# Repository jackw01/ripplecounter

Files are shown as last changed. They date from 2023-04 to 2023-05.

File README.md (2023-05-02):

# ripplecounter

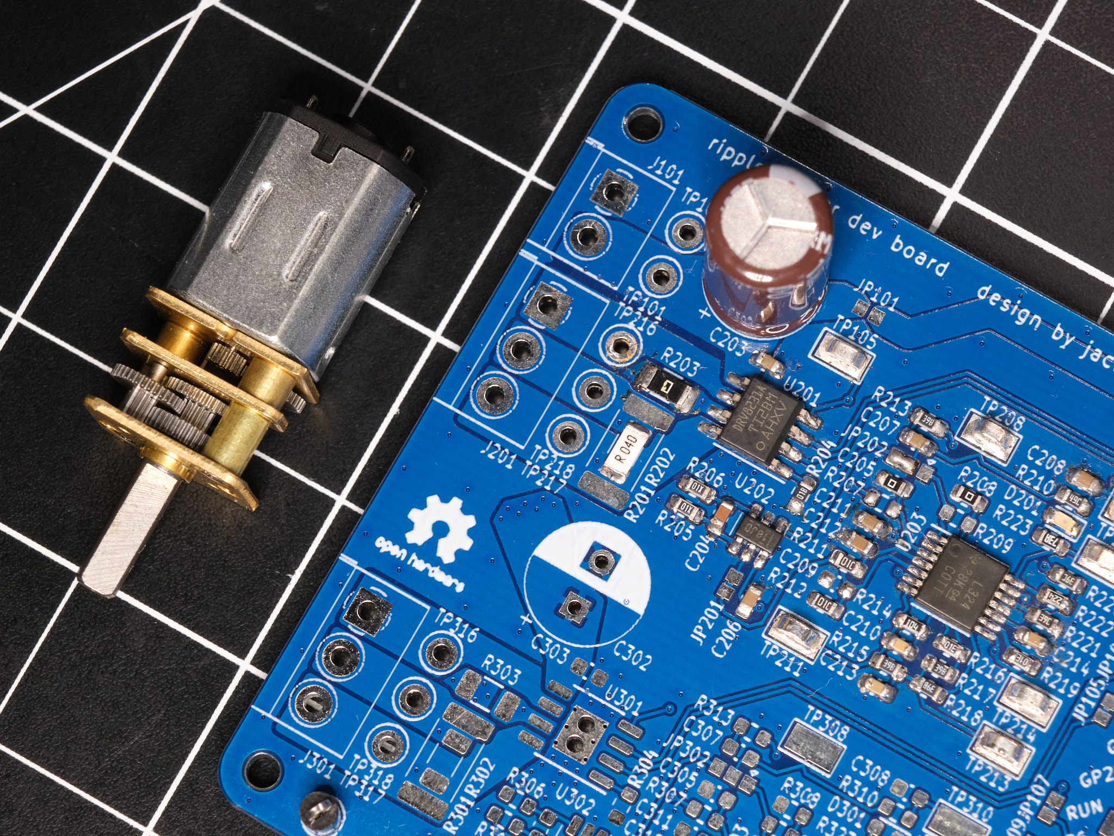
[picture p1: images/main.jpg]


## What?

* Control the position and speed of a brushed DC motor, *any* brushed DC motor
* No sensors, electromechanical components, or extra wiring needed
* Measure motor current with no extra complexity or cost
* Lower resolution than an encoder, but good enough for many applications
* Use almost any microcontroller, not just a Raspberry Pi Pico

### How Does It Work?

DC motors work internally by using a commutator and brushes, essentially a rotary switch that applies power to each of the motor’s coils in sequence as it rotates. By sensing, amplifying, and filtering the current flowing through the motor, the current ripples that occur as the motor rotates and each coil is energized can be counted by a microcontroller.

### How Well Does It Work?

If component values for the signal conditioning circuit are selected properly, surprisingly well.

## Circuit Design

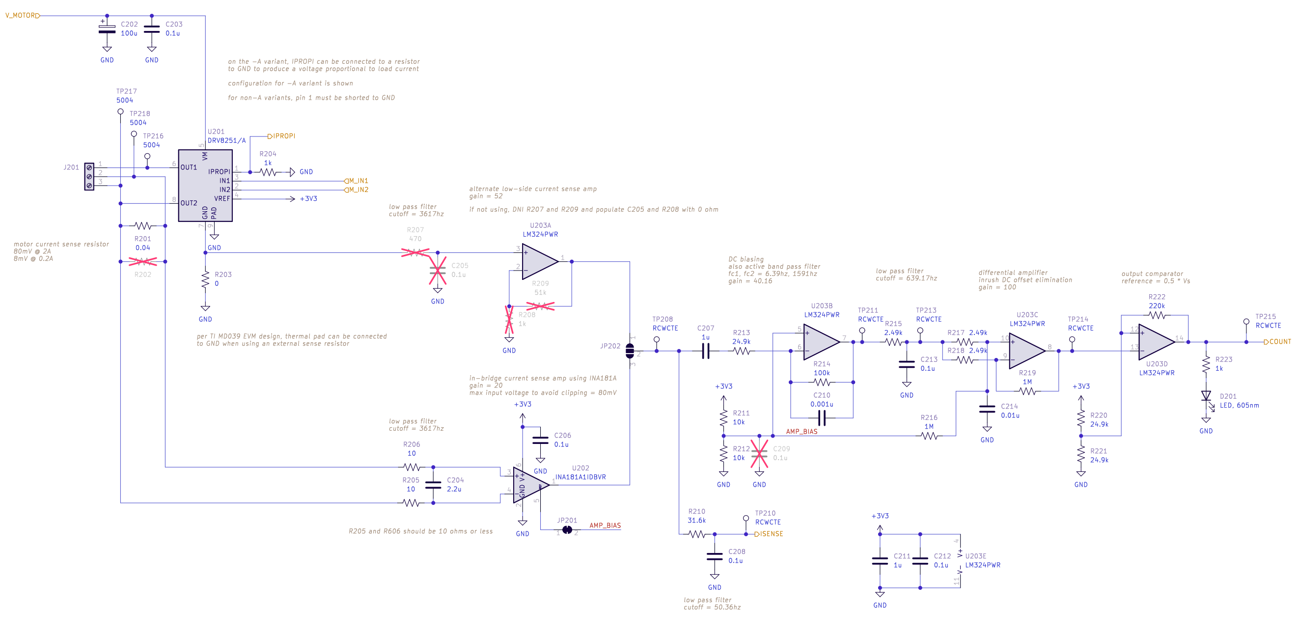
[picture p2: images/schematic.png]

[Schematic as PDF](pcb/schematic%20rev1%2020230427-01.pdf)

The signal conditioning circuit is based on the designs described in [Texas Instruments application note TIDA-01421](https://www.ti.com/lit/ug/tidud30a/tidud30a.pdf?ts=1682413672035) and [Microchip application note AN3049](http://ww1.microchip.com/downloads/en/Appnotes/Sensorless-Position-Control-of-Brushed-DC-Motor-Using-Ripple-Counting-Technique-00003049A.pdf). The initial current sense amplifier is implemented using the [Texas Instruments INA181 IC](https://www.mouser.com/datasheet/2/405/ina181-1109801.pdf) (U202) with a current sense resistor directly in series with the motor, allowing for bidirectional current sensing. The remaining amplifier and filtering stages are implemented using an LM324 (U203) general-purpose quad op amp. U203B is used as an active bandpass filter, which works with two other RC low-pass filters to eliminate high frequency noise and low-frequency oscillations in current caused by varying load on the motor. U203C is used to subtract large and relatively slow changes in the signal, such as the motor's inrush current spike. U203D is used as a comparator with hysteresis to generate a clean output signal.

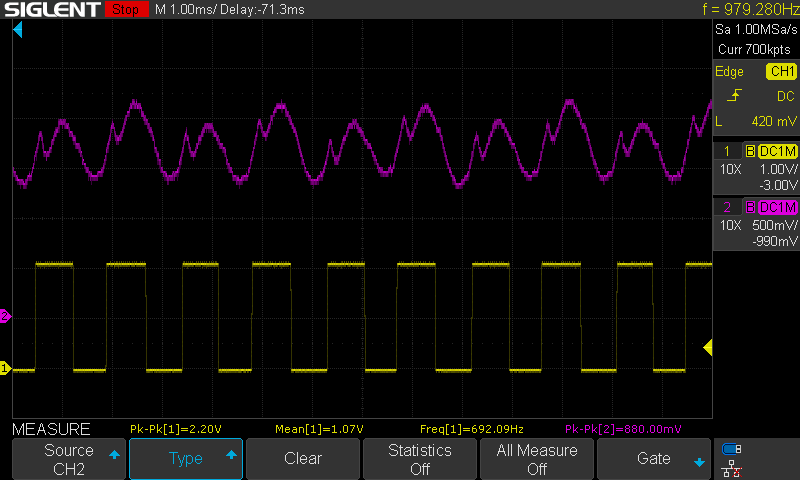
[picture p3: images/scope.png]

Purple: filtered, amplified motor current waveform (TP211); Yellow: output signal (TP215)

### Design Modification Guide

The component values used in this circuit will need to be adjusted for optimal performance with any motor - as-is, the values in the schematic were chosen for N20-size gearmotors and will work decently well for similar small motors.

When modifying the design for a different motor:

* The current sense resistor (R201/R202) value and power rating **must** be selected to keep the power dissipation in the resistor well within its specified power rating. For larger motors with high inrush/stall current, the pulse load capability of the resistor should also be considered.
* The current sense resistor value and the gain of the current sense amplifier (the INA181 IC used comes in four different fixed-gain options) **must** be selected to prevent clipping at the  output of the current sense amplifier with maximum motor current: `I_motor_max * R_isense * Gain < (3.3V / 2)`.

Several other components should be considered after choosing the sense resistor and amplifier:

* The gain of the active bandpass filter, set by R213 and R214, should be selected experimentally to minimize clipping at the output of the filter (TP211).
* The gain of the differential amplifier, set by R216-R219, should be selected experimentally to provide a clean output from the comparator (TP215). C214 should be changed if R217/R218 are changed by more than an order of magnitude.
* The cutoff frequencies of the active bandpass filter and the RC low-pass filter formed by R215 and C213 may need to be changed depending on the speed of the motor used. It is recommended that the cutoff frequency of R215/C213 be at least the motor's ripple frequency at full speed and the cutoff frequency of R214/C210 be at least two times that frequency.

## Development Board

The ripplecounter development board incorporates a Raspberry Pi Pico microcontroller, two motor drivers, and two copies of the signal conditioning circuit. The board is designed to allow the use of Texas Instruments DRV8231, DRV8231A, DRV8251, or DRV8251A SO-8 package H-bridge motor driver ICs, for up to 50V motor supply voltage and 4.1A peak output current. An external motor driver may also be used. The development board is designed to be manufactured by any low-cost PCB supplier, such as JLCPCB or PCBWay, and easily assembled and modified by hand - the smallest passive components used are 0603 size.

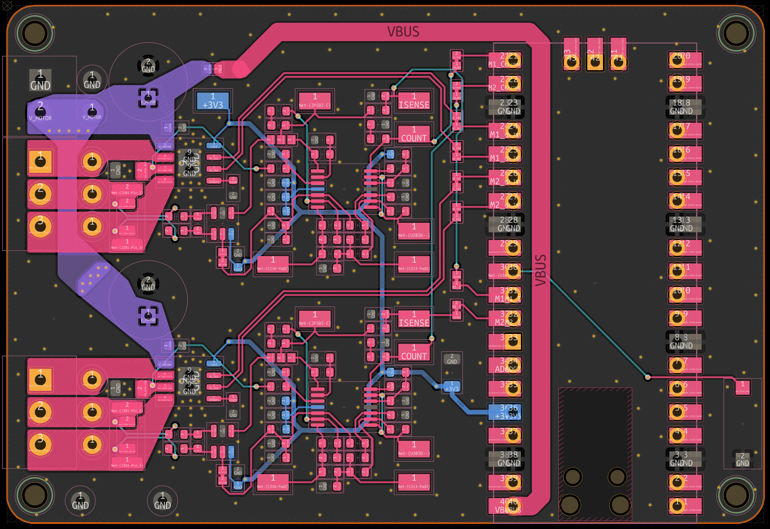
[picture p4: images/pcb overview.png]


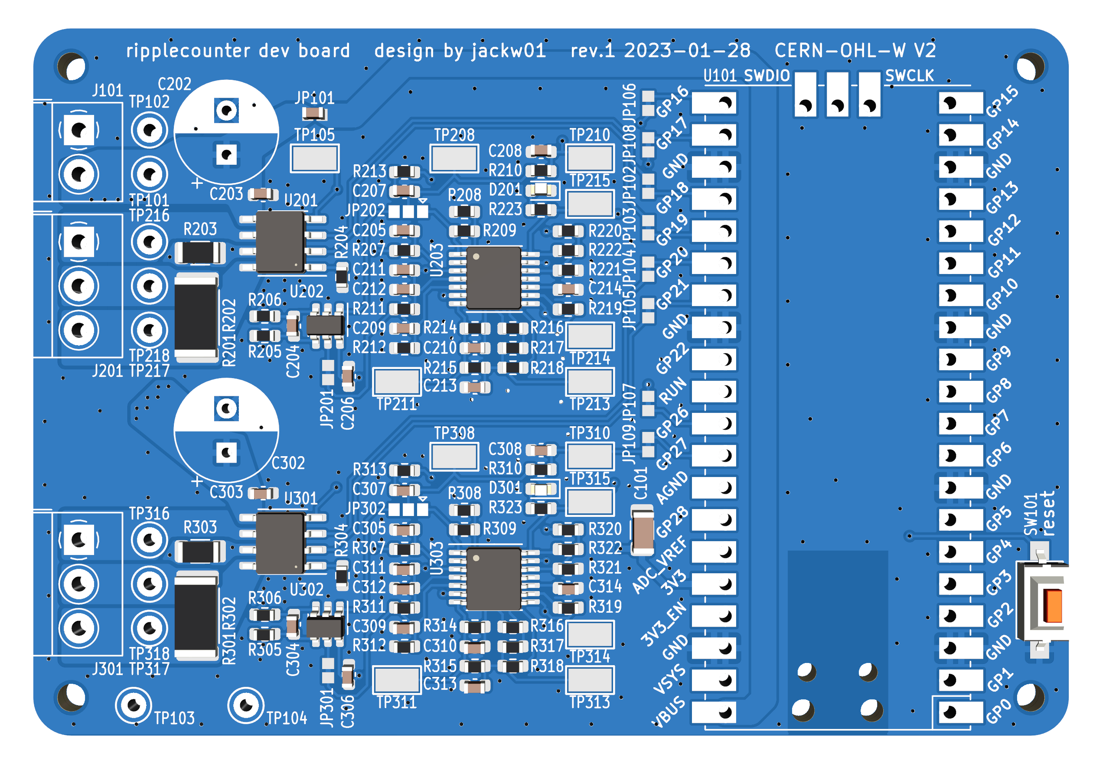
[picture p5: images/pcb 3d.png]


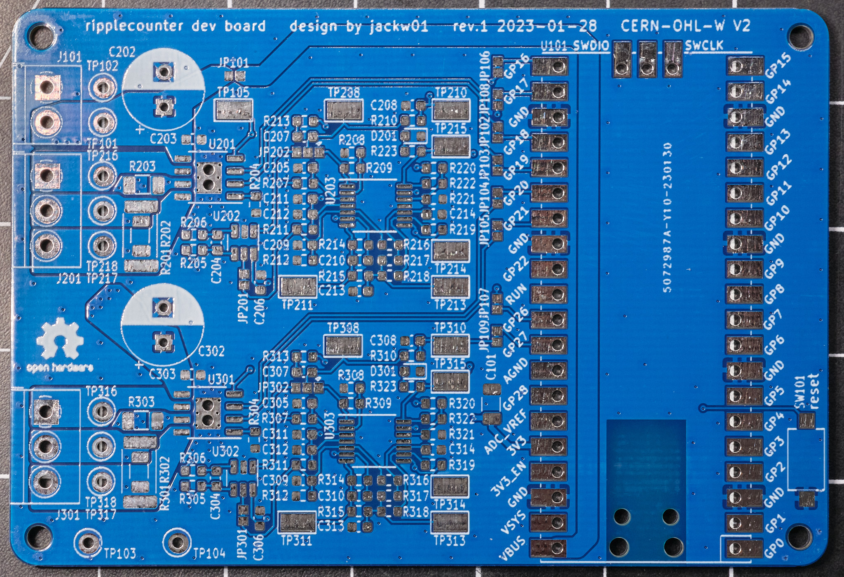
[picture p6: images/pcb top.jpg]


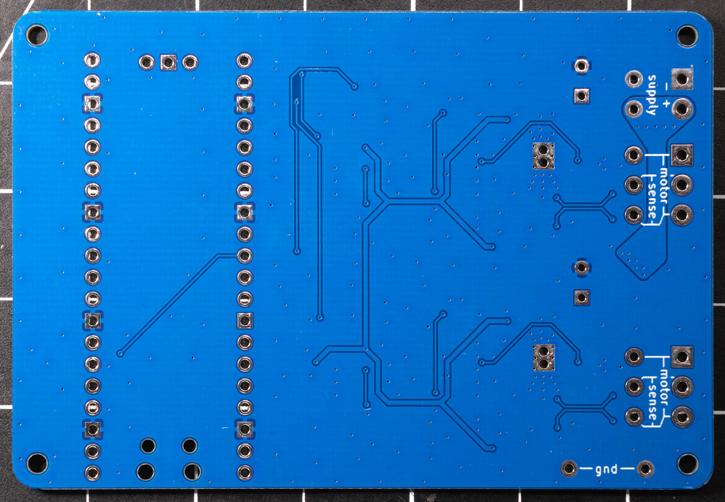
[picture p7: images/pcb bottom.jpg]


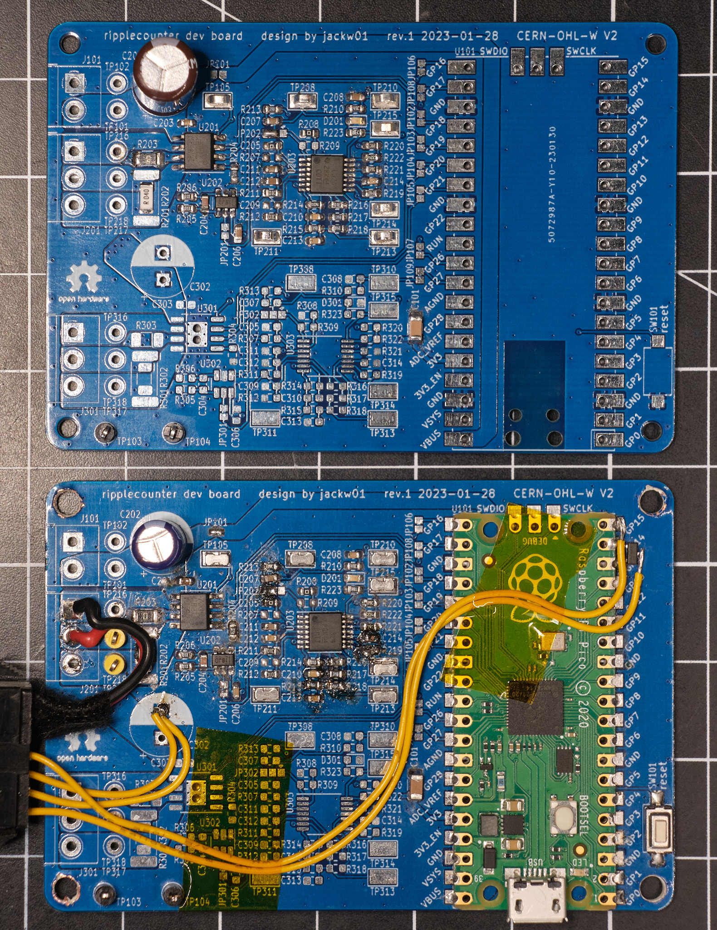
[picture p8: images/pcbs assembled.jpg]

The top PCB is minimally assembled for manually testing the signal conditioning circuit; the bottom PCB has been modified to control a camera slider for focus stacking macrophotography.

### License
The schematic is in the public domain - you are free to use this circuit design for any purpose, without attribution. The PCB layout and Gerber files for the development board  are released under the CERN Open Hardware Licence Version 2 - Weakly Reciprocal (CERN-OHL-W V2).

## Firmware

Basic firmware using the Raspberry Pi Pico C SDK is provided, which moves the motor while printing the position, speed, and current draw via UART. All important constants are documented in `ripplecounter_motor.c`.

Note: When used with the DRV8x21 motor controller on the development board, this firmware brakes the motor (as opposed to letting it coast) when it is not running, which is desirable for applications that require position control. If the motor is forcibly rotated while it is not running, the change in position will be detected via the ripple counter circuit, but sensing the *direction* of rotation is not implemented. If this functionality is needed, it can be implemented by sampling the motor current value read through the ADC, which will be negative or positive depending on which direction the motor is being turned.

### License

All code provided is released under the MIT License.

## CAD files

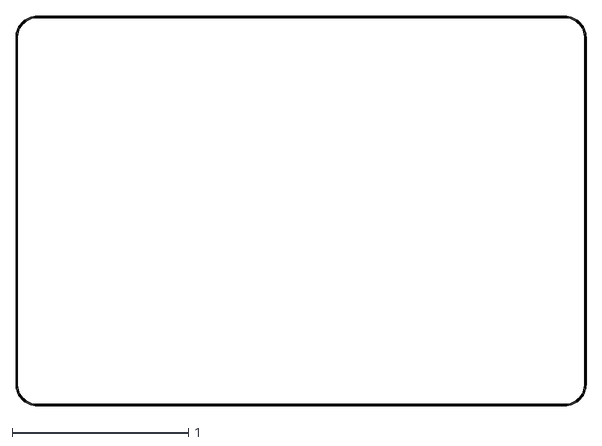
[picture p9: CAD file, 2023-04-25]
pcb/gerber rev1/ripplecounter-Edge_Cuts.dxf
3.24 x 2.21

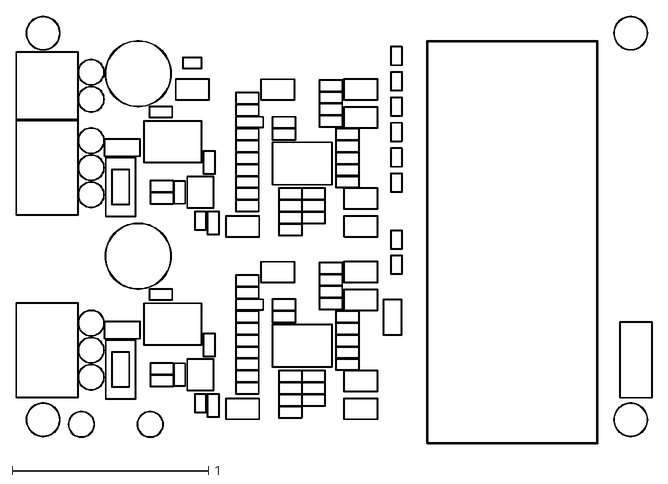
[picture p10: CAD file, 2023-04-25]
pcb/gerber rev1/ripplecounter-F_Courtyard.dxf
3.24 x 2.18

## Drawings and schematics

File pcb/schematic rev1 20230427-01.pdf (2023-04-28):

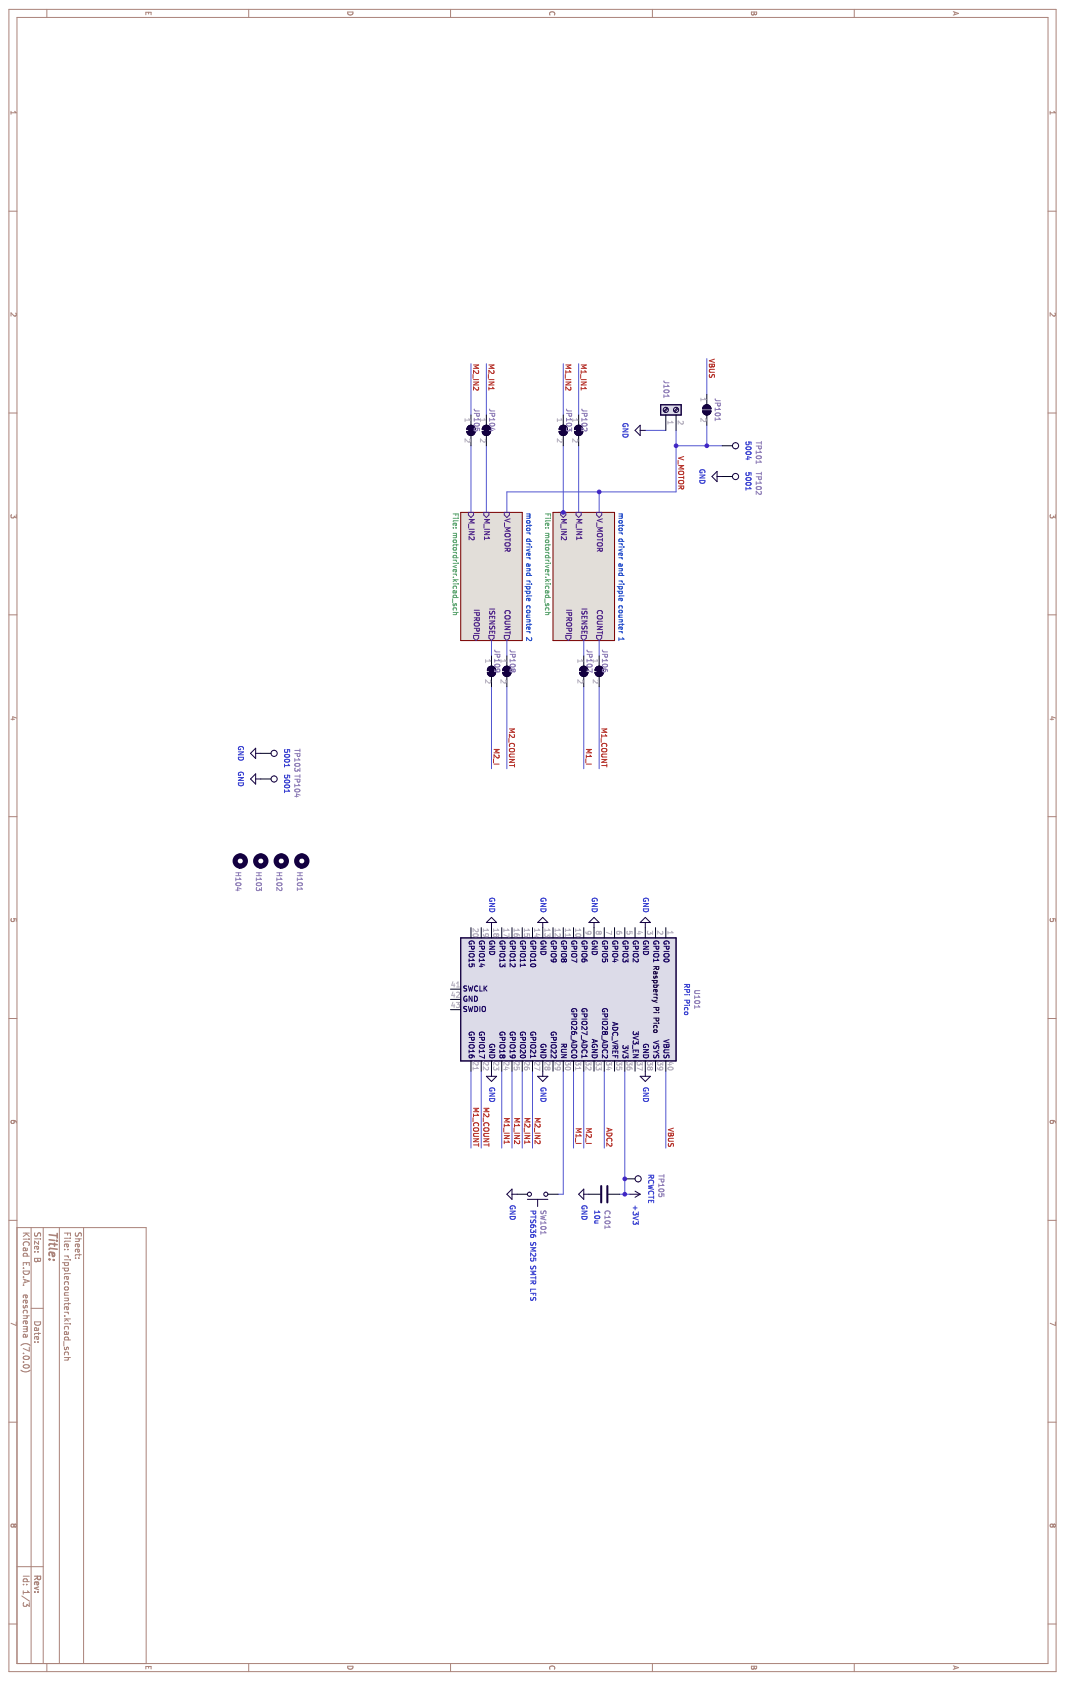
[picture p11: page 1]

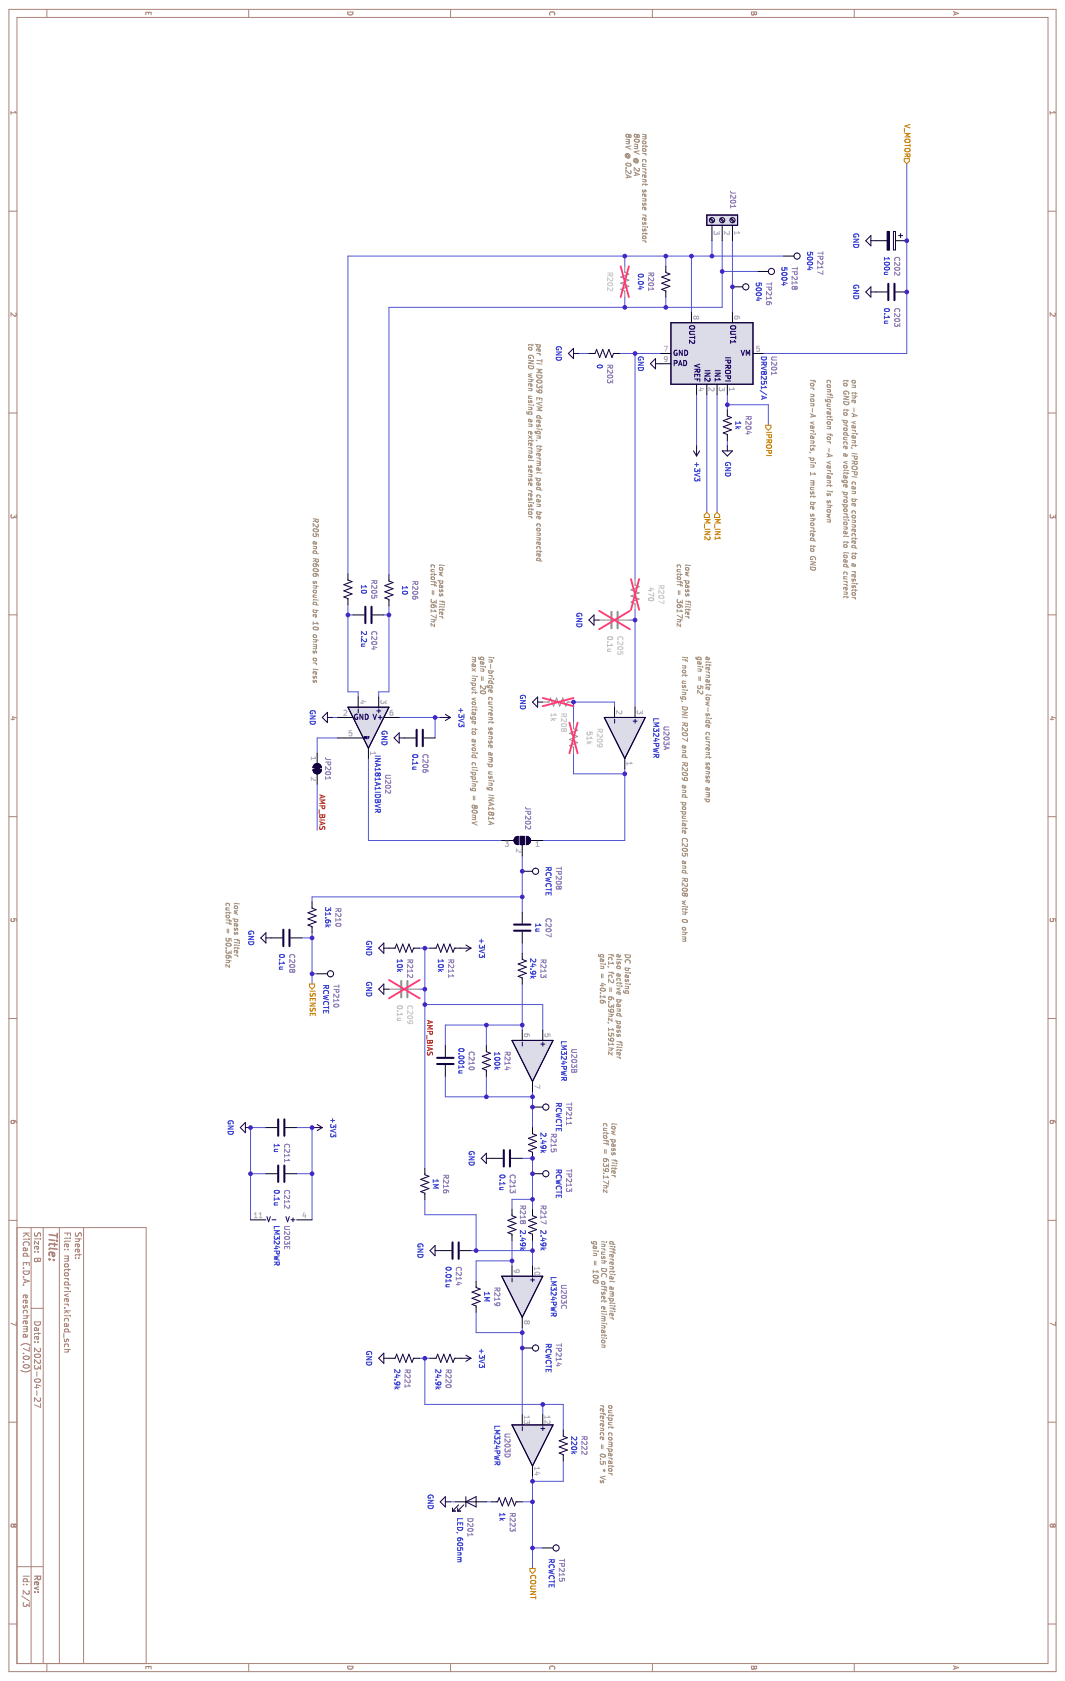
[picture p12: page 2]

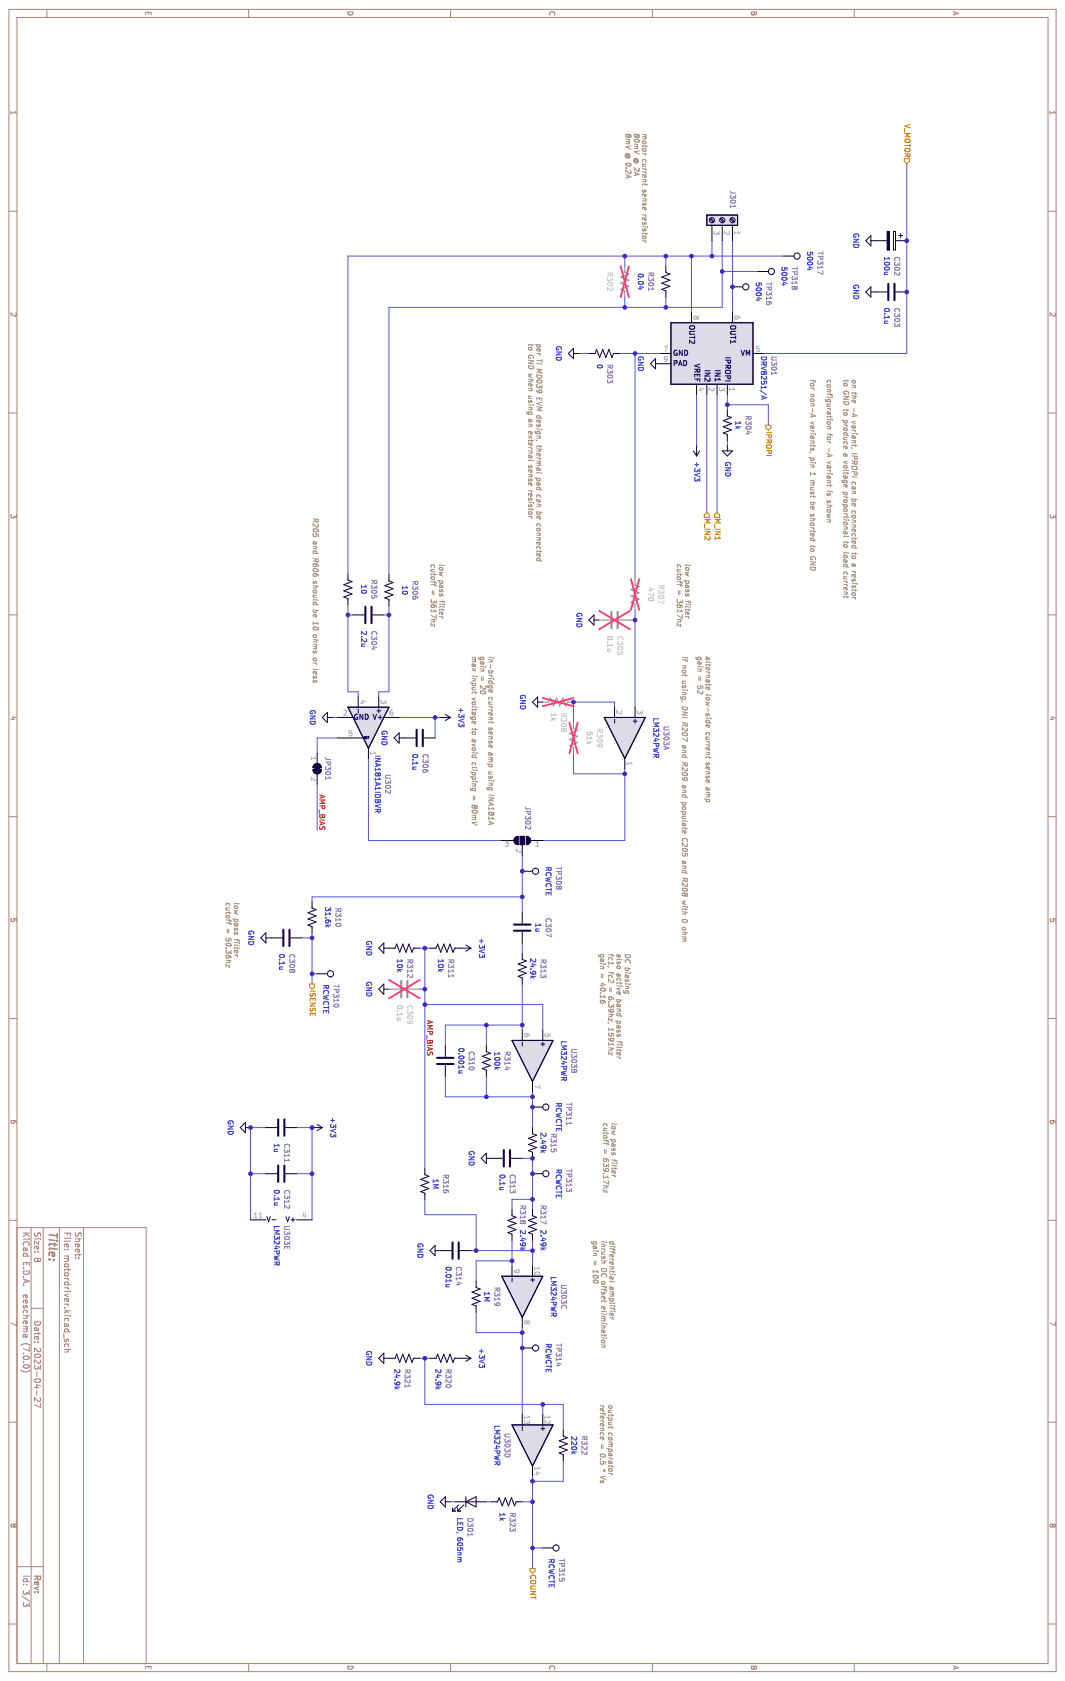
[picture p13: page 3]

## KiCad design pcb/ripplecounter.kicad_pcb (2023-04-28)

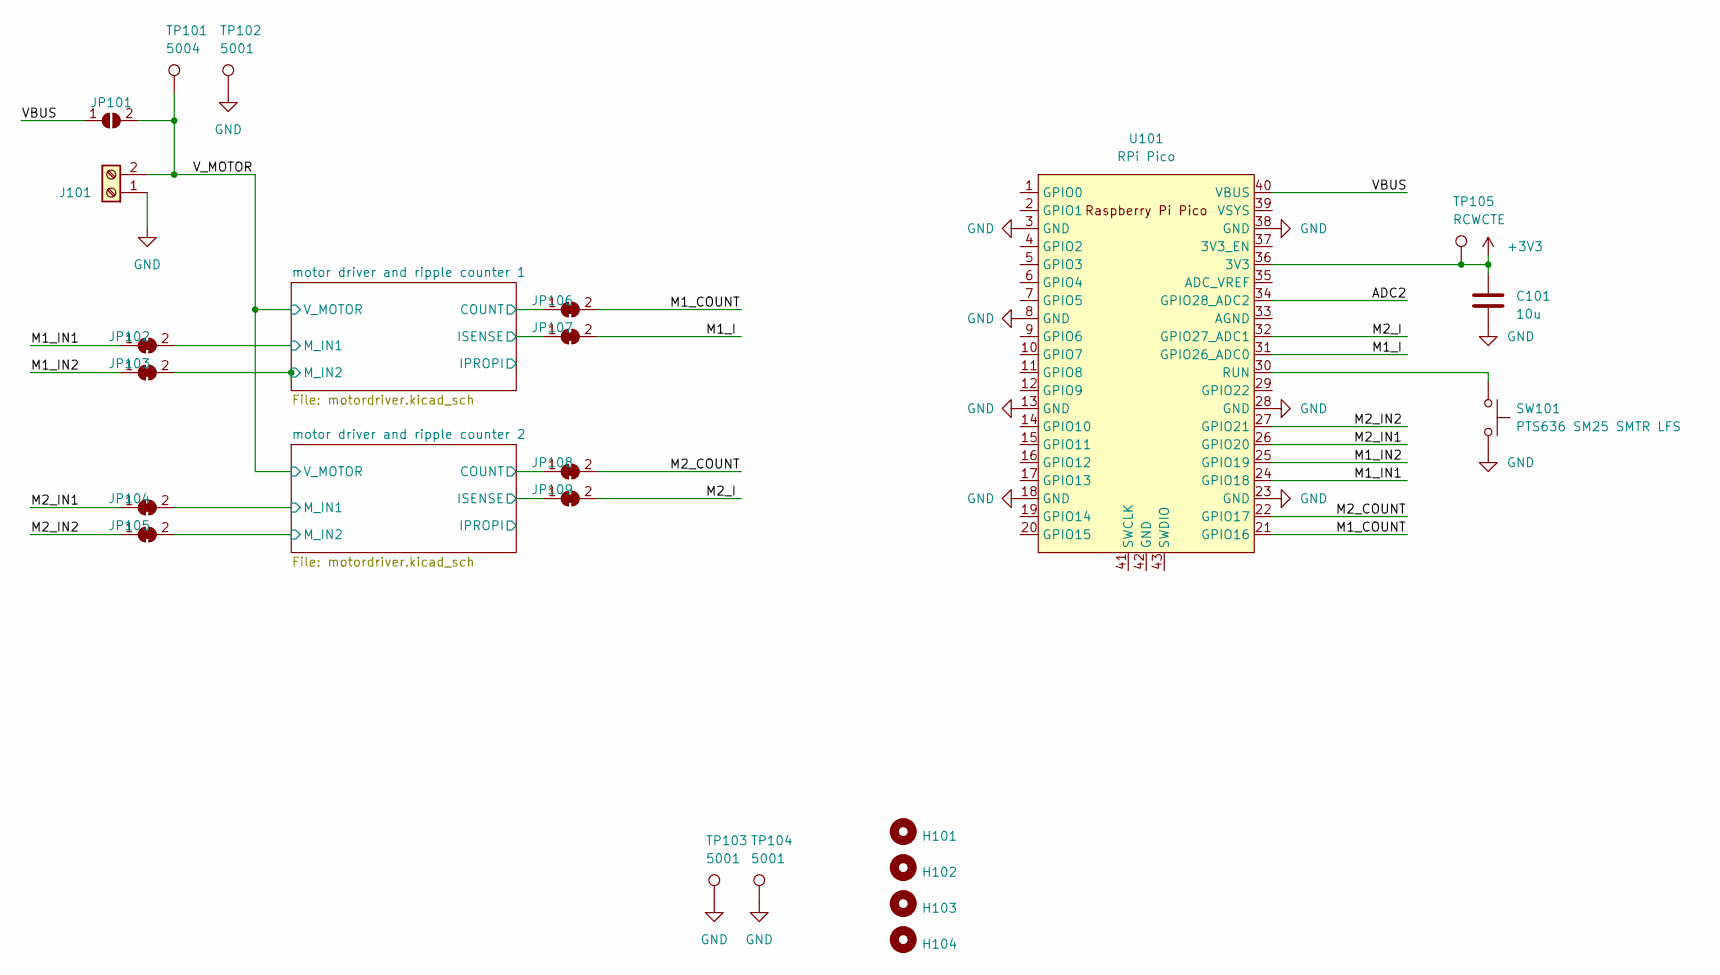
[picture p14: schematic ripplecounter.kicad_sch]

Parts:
C101: 10u; C_1206_3216Metric
H101, H102, H103, H104: MountingHole_2.2mm_M2_ISO14580
J101: TerminalBlock_4Ucon_1x02_P3.50mm_Horizontal
JP101: Jumper_0603
JP102, JP103, JP106, JP107, JP108, JP109: Jumper_0603_Bridged
JP104, JP105: 0603_Closed; Jumper_0603_Bridged
SW101: PTS636 SM25 SMTR LFS; SW_SPST_CK_RS282G05A3
TP101: 5004; TestPoint_Keystone_5000-5004_Miniature
TP102, TP103, TP104: 5001; TestPoint_Keystone_5000-5004_Miniature
TP105: RCWCTE; TestPoint_Keystone_5015_Micro-Minature
U101: RPi Pico; RPi_Pico_SMD_TH

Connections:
+3V3: C101.1, TP105.1, U101.36 (3V3); also elsewhere on the board
/ADC2: U101.34 (GPIO28_ADC2)
/M1_COUNT: JP106.2 (B), U101.21 (GPIO16)
/M1_I: JP107.2 (B), U101.31 (GPIO26_ADC0)
/M1_IN1: JP102.1 (A), U101.24 (GPIO18)
/M1_IN2: JP103.1 (A), U101.25 (GPIO19)
/M2_COUNT: JP108.2 (B), U101.22 (GPIO17)
/M2_I: JP109.2 (B), U101.32 (GPIO27_ADC1)
/M2_IN1: JP104.1 (A), U101.26 (GPIO20)
/M2_IN2: JP105.1 (A), U101.27 (GPIO21)
/VBUS: JP101.1 (A), U101.40 (VBUS)
/V_MOTOR: J101.2, JP101.2 (B), TP101.1; also elsewhere on the board
/motor driver and ripple counter 1/COUNT: JP106.1 (A); also elsewhere on the board
/motor driver and ripple counter 1/ISENSE: JP107.1 (A); also elsewhere on the board
/motor driver and ripple counter 1/M_IN1: JP102.2 (B); also elsewhere on the board
/motor driver and ripple counter 1/M_IN2: JP103.2 (B); also elsewhere on the board
/motor driver and ripple counter 2/COUNT: JP108.1 (A); also elsewhere on the board
/motor driver and ripple counter 2/ISENSE: JP109.1 (A); also elsewhere on the board
/motor driver and ripple counter 2/M_IN1: JP104.2 (B); also elsewhere on the board
/motor driver and ripple counter 2/M_IN2: JP105.2 (B); also elsewhere on the board
GND: C101.2, J101.1, SW101.2, TP102.1, TP103.1, TP104.1, U101.3 (GND), U101.8 (GND), U101.13 (GND), U101.18 (GND), U101.23 (GND), U101.28 (GND), U101.38 (GND); also elsewhere on the board
unnamed: SW101.1, U101.30 (RUN)

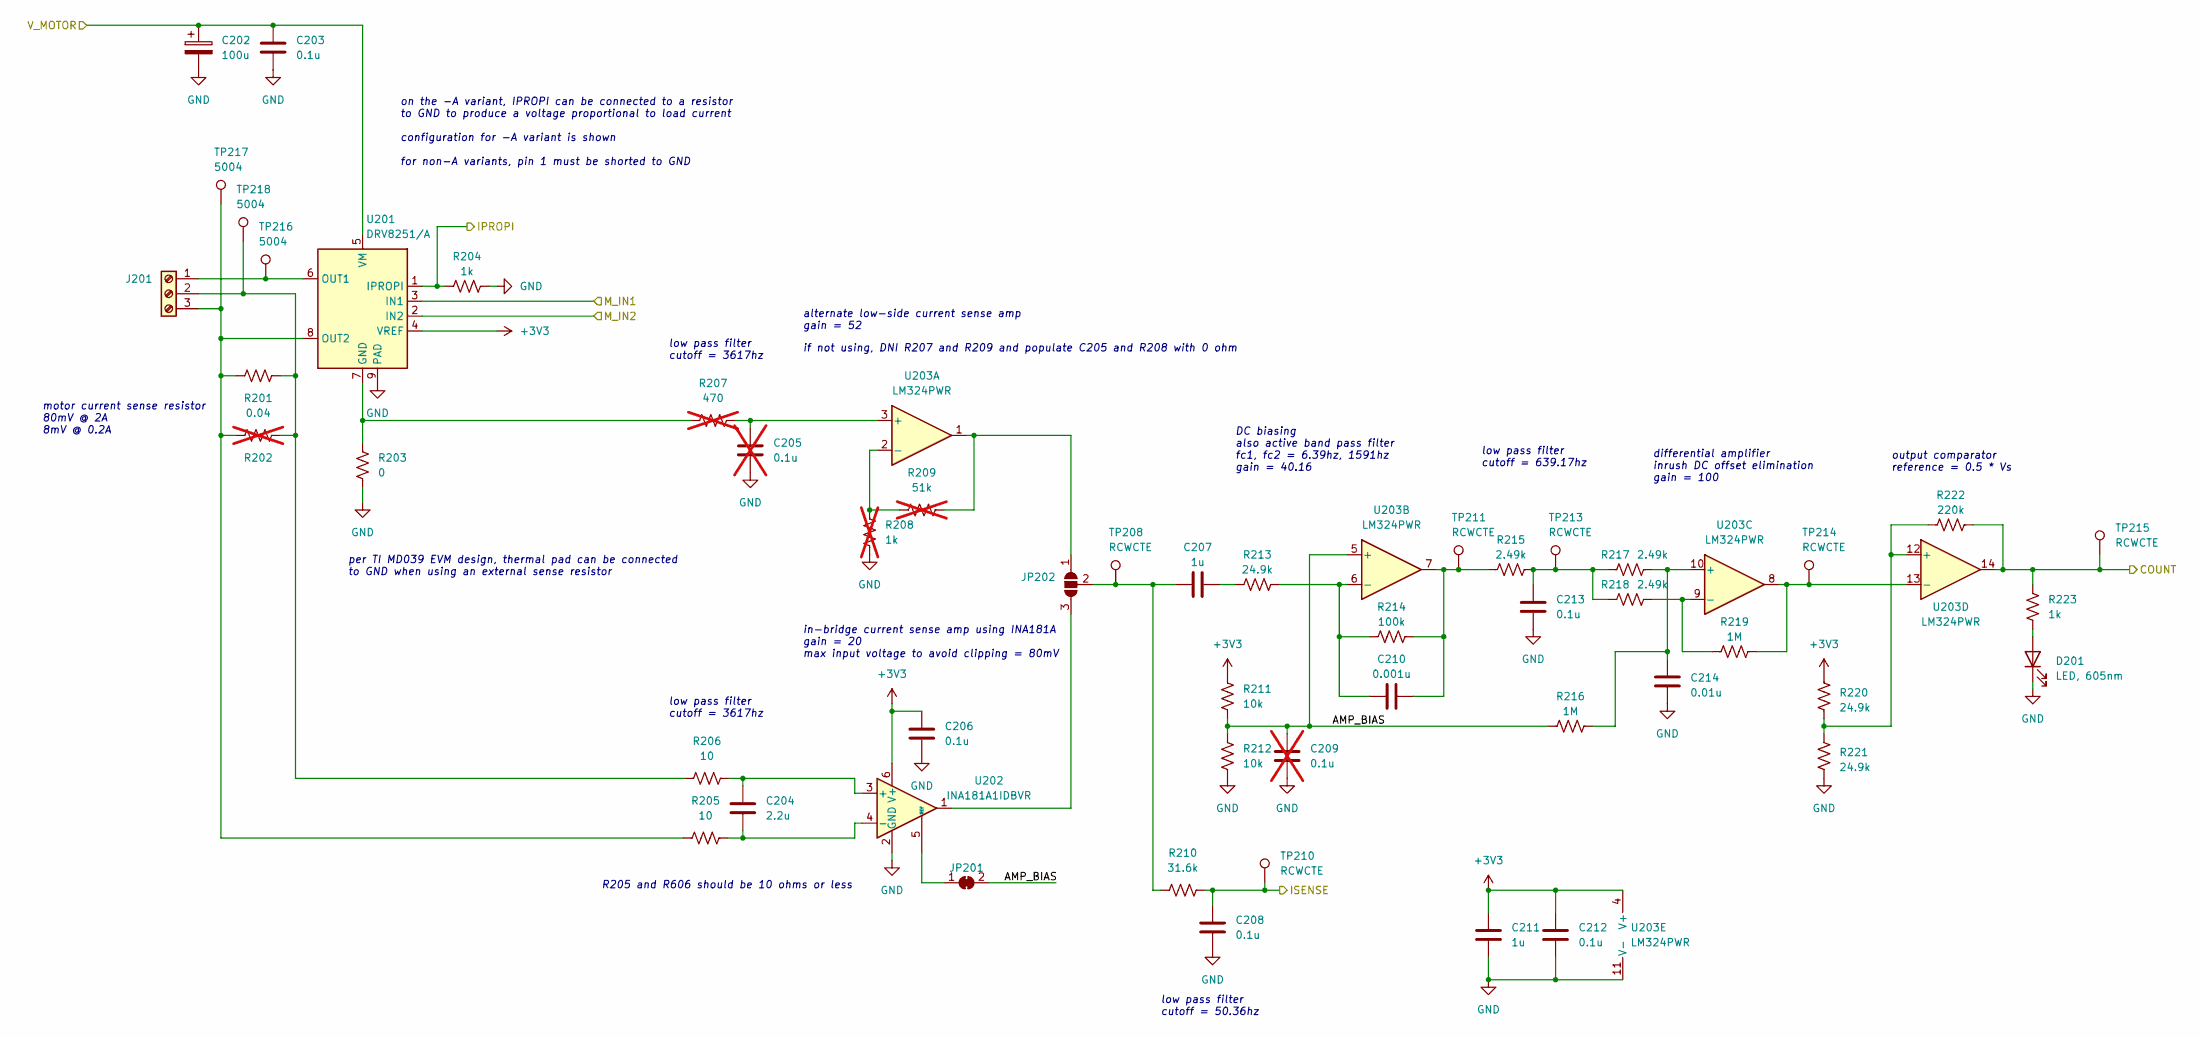
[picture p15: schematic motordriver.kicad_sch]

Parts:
C202: 100u; CP_Radial_D8.0mm_P3.50mm
C203, C206, C208, C212, C213: 0.1u; C_0603_1608Metric
C204: 2.2u; C_0603_1608Metric
C205, C209: 0.1u; C_0603_1608Metric; not fitted
C207, C211: 1u; C_0603_1608Metric
C210: 0.001u; C_0603_1608Metric
C214: 0.01u; C_0603_1608Metric
D201: LED, 605nm; LED_0603_1608Metric
J201: TerminalBlock_4Ucon_1x03_P3.50mm_Horizontal
JP201: Jumper_0603_Bridged
JP202: Bi_0603_Open
R201: 0.04; R_1206_3216Metric
R202: R_2512_6332Metric; not fitted
R203: 0; R_1206_3216Metric
R204, R223: 1k; R_0603_1608Metric
R205, R206: 10; R_0603_1608Metric
R207: 470; R_0603_1608Metric; not fitted
R208: 1k; R_0603_1608Metric; not fitted
R209: 51k; R_0603_1608Metric; not fitted
R210: 31.6k; R_0603_1608Metric
R211, R212: 10k; R_0603_1608Metric
R213, R220, R221: 24.9k; R_0603_1608Metric
R214: 100k; R_0603_1608Metric
R215, R217, R218: 2.49k; R_0603_1608Metric
R216, R219: 1M; R_0603_1608Metric
R222: 220k; R_0603_1608Metric
TP208, TP210, TP211, TP213, TP214, TP215: RCWCTE; TestPoint_Keystone_5015_Micro-Minature
TP216, TP217, TP218: 5004; TestPoint_Keystone_5000-5004_Miniature
U201: DRV8251/A; HSOP-8-1EP_3.9x4.9mm_P1.27mm_EP2.41x3.1mm_ThermalVias_HandS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
U202: INA181A1IDBVR; SOT-23-6
U203: LM324PWR; TSSOP-14_4.4x5mm_P0.65mm

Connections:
+3V3: C206.1, C211.1, C212.1, R211.1, R220.1, U201.4 (VREF), U202.6 (V+), U203.4 (V+); also elsewhere on the board
/V_MOTOR: C202.1, C203.1, U201.5 (VM); also elsewhere on the board
/motor driver and ripple counter 1/AMP_BIAS: C209.2, JP201.2 (B), R211.2, R212.1, R216.2, U203.5 (+)
/motor driver and ripple counter 1/COUNT: R222.1, R223.1, TP215.1, U203.14; also elsewhere on the board
/motor driver and ripple counter 1/IPROPI: R204.1, U201.1 (IPROPI)
/motor driver and ripple counter 1/ISENSE: C208.2, R210.2, TP210.1; also elsewhere on the board
/motor driver and ripple counter 1/M_IN1: U201.3 (IN1); also elsewhere on the board
/motor driver and ripple counter 1/M_IN2: U201.2 (IN2); also elsewhere on the board
GND: C202.2, C203.2, C205.2, C206.2, C208.1, C209.1, C211.2, C212.2, C213.1, C214.1, D201.1 (K), R203.1, R204.2, R208.2, R212.2, R221.2, U201.9 (PAD), U202.2 (GND), U203.11 (V-); also elsewhere on the board
unnamed: C207.2, R213.1
unnamed: C210.2, R214.1, R215.1, TP211.1, U203.7
unnamed: C213.2, R215.2, R217.1, R218.1, TP213.1
unnamed: D201.2 (A), R223.2
unnamed: J201.1, TP216.1, U201.6 (OUT1)
unnamed: J201.2, R201.2, R202.2, R206.2, TP218.1
unnamed: J201.3, R201.1, R202.1, R205.2, TP217.1, U201.8 (OUT2)
unnamed: JP201.1 (A), U202.5 (REF)
unnamed: JP202.1 (A), R209.1, U203.1
unnamed: JP202.3 (B), U202.1
unnamed: C207.1, JP202.2 (C), R210.1, TP208.1
unnamed: R203.2, R207.2, U201.7 (GND)
unnamed: C204.1, R206.1, U202.3 (+)
unnamed: C204.2, R205.1, U202.4 (-)
unnamed: C205.1, R207.1, U203.3 (+)
unnamed: R208.1, R209.2, U203.2 (-)
unnamed: C210.1, R213.2, R214.2, U203.6 (-)
unnamed: C214.2, R216.1, R217.2, U203.10 (+)
unnamed: R218.2, R219.2, U203.9 (-)
unnamed: R220.2, R221.1, R222.2, U203.12 (+)
unnamed: R219.1, TP214.1, U203.8, U203.13 (-)

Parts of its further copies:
C302: 100u; CP_Radial_D8.0mm_P3.50mm
C303, C306, C308, C312, C313: 0.1u; C_0603_1608Metric
C304: 2.2u; C_0603_1608Metric
C305, C309: 0.1u; C_0603_1608Metric; not fitted
C307, C311: 1u; C_0603_1608Metric
C310: 0.001u; C_0603_1608Metric
C314: 0.01u; C_0603_1608Metric
D301: LED, 605nm; LED_0603_1608Metric
J301: TerminalBlock_4Ucon_1x03_P3.50mm_Horizontal
JP301: Jumper_0603_Bridged
JP302: Bi_0603_Open
R301: 0.04; R_1206_3216Metric
R302: R_2512_6332Metric; not fitted
R303: 0; R_1206_3216Metric
R304, R323: 1k; R_0603_1608Metric
R305, R306: 10; R_0603_1608Metric
R307: 470; R_0603_1608Metric; not fitted
R308: 1k; R_0603_1608Metric; not fitted
R309: 51k; R_0603_1608Metric; not fitted
R310: 31.6k; R_0603_1608Metric
R311, R312: 10k; R_0603_1608Metric
R313, R320, R321: 24.9k; R_0603_1608Metric
R314: 100k; R_0603_1608Metric
R315, R317, R318: 2.49k; R_0603_1608Metric
R316, R319: 1M; R_0603_1608Metric
R322: 220k; R_0603_1608Metric
TP308, TP310, TP311, TP313, TP314, TP315: RCWCTE; TestPoint_Keystone_5015_Micro-Minature
TP316, TP317, TP318: 5004; TestPoint_Keystone_5000-5004_Miniature
U301: DRV8251/A; HSOP-8-1EP_3.9x4.9mm_P1.27mm_EP2.41x3.1mm_ThermalVias_HandS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
U302: INA181A1IDBVR; SOT-23-6
U303: LM324PWR; TSSOP-14_4.4x5mm_P0.65mm

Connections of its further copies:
+3V3: C306.1, C311.1, C312.1, R311.1, R320.1, U301.4 (VREF), U302.6 (V+), U303.4 (V+); also elsewhere on the board
/V_MOTOR: C302.1, C303.1, U301.5 (VM); also elsewhere on the board
/motor driver and ripple counter 2/AMP_BIAS: C309.2, JP301.2 (B), R311.2, R312.1, R316.2, U303.5 (+)
/motor driver and ripple counter 2/COUNT: R322.1, R323.1, TP315.1, U303.14; also elsewhere on the board
/motor driver and ripple counter 2/IPROPI: R304.1, U301.1 (IPROPI)
/motor driver and ripple counter 2/ISENSE: C308.2, R310.2, TP310.1; also elsewhere on the board
/motor driver and ripple counter 2/M_IN1: U301.3 (IN1); also elsewhere on the board
/motor driver and ripple counter 2/M_IN2: U301.2 (IN2); also elsewhere on the board
GND: C302.2, C303.2, C305.2, C306.2, C308.1, C309.1, C311.2, C312.2, C313.1, C314.1, D301.1 (K), R303.1, R304.2, R308.2, R312.2, R321.2, U301.9 (PAD), U302.2 (GND), U303.11 (V-); also elsewhere on the board
unnamed: C307.2, R313.1
unnamed: C310.2, R314.1, R315.1, TP311.1, U303.7
unnamed: C313.2, R315.2, R317.1, R318.1, TP313.1
unnamed: D301.2 (A), R323.2
unnamed: J301.1, TP316.1, U301.6 (OUT1)
unnamed: J301.2, R301.2, R302.2, R306.2, TP318.1
unnamed: J301.3, R301.1, R302.1, R305.2, TP317.1, U301.8 (OUT2)
unnamed: JP301.1 (A), U302.5 (REF)
unnamed: JP302.1 (A), R309.1, U303.1
unnamed: JP302.3 (B), U302.1
unnamed: C307.1, JP302.2 (C), R310.1, TP308.1
unnamed: R303.2, R307.2, U301.7 (GND)
unnamed: C304.1, R306.1, U302.3 (+)
unnamed: C304.2, R305.1, U302.4 (-)
unnamed: C305.1, R307.1, U303.3 (+)
unnamed: R308.1, R309.2, U303.2 (-)
unnamed: C310.1, R313.2, R314.2, U303.6 (-)
unnamed: C314.2, R316.1, R317.2, U303.10 (+)
unnamed: R318.2, R319.2, U303.9 (-)
unnamed: R320.2, R321.1, R322.2, U303.12 (+)
unnamed: R319.1, TP314.1, U303.8, U303.13 (-)

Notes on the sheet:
low pass filter cutoff = 50.36hz
low pass filter cutoff = 3617hz
DC biasing also active band pass filter fc1, fc2 = 6.39hz, 1591hz gain = 40.16
low pass filter cutoff = 3617hz
if not using, DNI R207 and R209 and populate C205 and R208 with 0 ohm
alternate low-side current sense amp gain = 52
low pass filter cutoff = 639.17hz
motor current sense resistor 80mV @ 2A 8mV @ 0.2A
per TI MD039 EVM design, thermal pad can be connected to GND when using an external sense resistor
in-bridge current sense amp using INA181A gain = 20 max input voltage to avoid clipping = 80mV
differential amplifier inrush DC offset elimination gain = 100
R205 and R606 should be 10 ohms or less
output comparator reference = 0.5 * Vs
on the -A variant, IPROPI can be connected to a resistor to GND to produce a voltage proportional to load current configuration for -A variant is shown for non-A variants, pin 1 must be shorted to GND

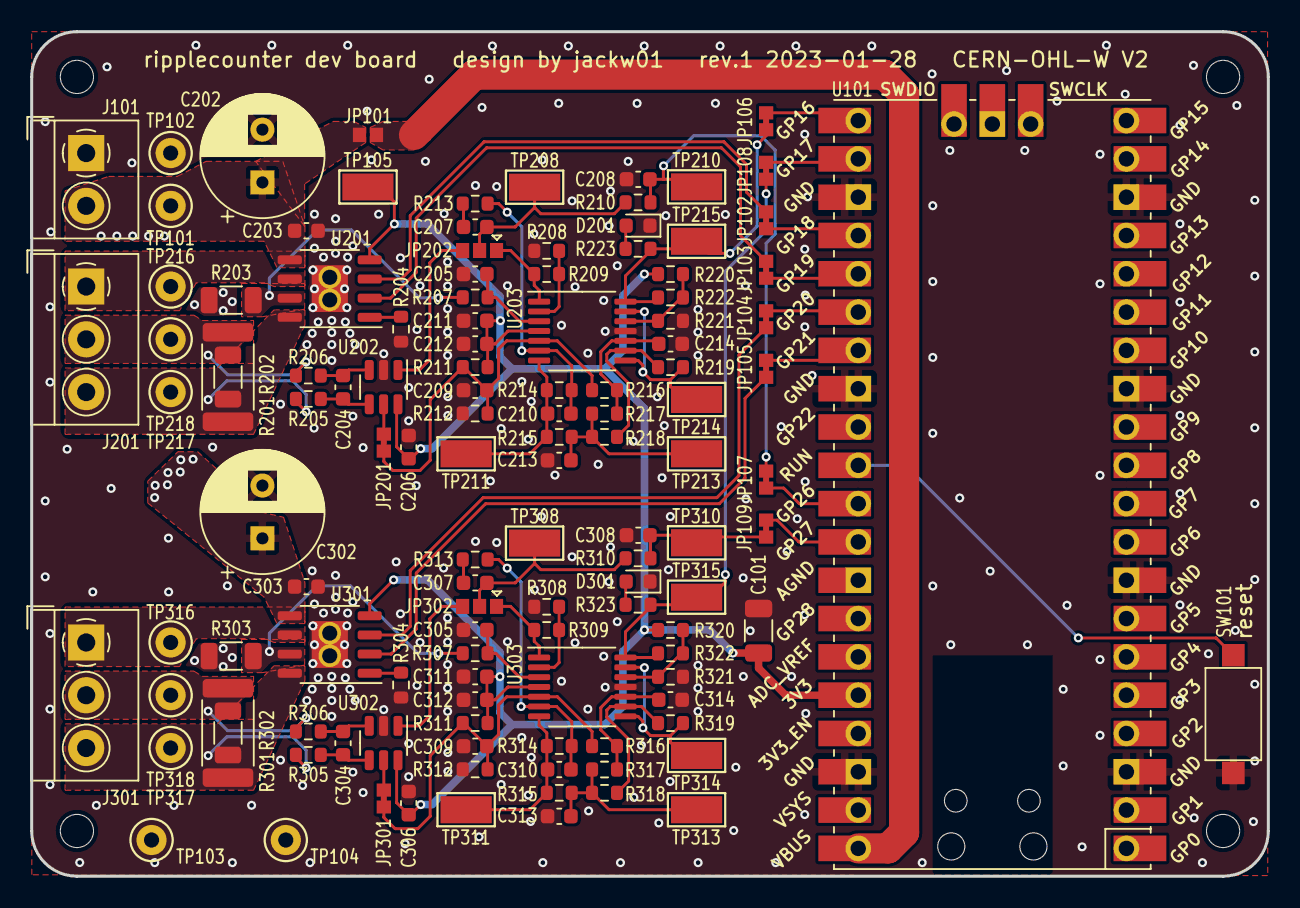
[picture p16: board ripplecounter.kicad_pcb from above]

Board: 2 copper layers, 82.0 x 56.0 mm, 126 parts (0 on the bottom side), 67 nets.

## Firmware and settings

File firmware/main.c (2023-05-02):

#include <stdio.h>
#include <math.h>

#include "pico/stdlib.h"
#include "hardware/gpio.h"

#include "ripplecounter_motor.h"


static const uint32_t TickIntervalUs = 1000;

static const uint32_t MotorMeasurementIntervalMs = 100;
static const uint32_t StateChangeIntervalMs = 2000;

enum SystemState {
    SystemStateInit = 0,
    SystemStateIdle,
    SystemStateForward,
    SystemStateReverse
};

uint32_t system_state = SystemStateInit;

uint32_t motor_power = 0;
uint32_t motor_measurement_timer = 1;
uint32_t state_timer = 1;
int32_t last_position = 0;


// Main loop

void tick(uint32_t millis, uint32_t dt_micros) {
  if (millis >= motor_measurement_timer) {
    int32_t position = ripplecounter_get_position_counts();
    int32_t delta_position = position - last_position;

    printf("motor current (mA): %d\n", ripplecounter_get_current_ma());
    printf("position (counts): %d\n", position);
    printf("speed (counts/s): %d\n\n", (delta_position > 0 ? delta_position : -delta_position) * 1000 / MotorMeasurementIntervalMs);

    motor_measurement_timer = millis + MotorMeasurementIntervalMs;
    last_position = position;
  }

  if (system_state == SystemStateInit) {
    motor_set_direction(true);
    motor_set_power(0);
    system_state = SystemStateForward;
  } else if (system_state == SystemStateForward) {
    if (millis >= state_timer) {
      system_state = SystemStateReverse;
      state_timer = millis + StateChangeIntervalMs;
      motor_set_direction(true);
      motor_set_power(motor_power);
    }
  } else if (system_state == SystemStateReverse) {
    if (millis >= state_timer) {
      system_state = SystemStateForward;
      state_timer = millis + StateChangeIntervalMs;
      motor_set_direction(false);
      motor_set_power(motor_power);
    }
  }
}

int main() {
  stdio_init_all();

  ripplecounter_motor_init();
  motor_power = motor_get_max_power();

  uint64_t micros;
  uint32_t dt;

  while (true) {
    micros = time_us_64();
    tick(us_to_ms(micros), dt);
    dt = time_us_64() - micros;
    if (dt < TickIntervalUs) {
      absolute_time_t target;
      update_us_since_boot(&target, micros + TickIntervalUs);
      busy_wait_until(target);
    }
  }
}

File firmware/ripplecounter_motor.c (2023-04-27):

#include <math.h>

#include "pico/stdlib.h"
#include "hardware/gpio.h"
#include "hardware/pwm.h"
#include "hardware/adc.h"

#include "ripplecounter_motor.h"


// Pin assignments for rev.1 ripplecounter dev board

// ADC input connected to low pass filtered current sense signal
static const uint32_t PinMotorISense = 26;

// Motor driver PWM pins
static const uint32_t PinMotorA = 18;
static const uint32_t PinMotorB = 19;

// Counter input
static const uint32_t PinCounterIn = 16;

// PWM max value
static const uint32_t PWMWrap = 8000;

// Current sense gain
// = R_Isense * gain * 10000
static const int32_t CurrentSenseGain = 8000;

// Debouncing
// If enabled, pulses will only be counted if they are the first
// pulse after a period of inactivity, or if their length is
// more than x percent of the length of the previous pulse
static const bool EnableDebouncing = true;
static const uint32_t InactivityThresholdUs = 20000;
static const uint32_t DebounceThresholdPercent = 60;


static uint32_t slice;

static int32_t ripplecounter_position = 0;
static uint32_t ripplecounter_last_time = 0;
static uint32_t ripplecounter_last_dt = 0;

static bool ripplecounter_direction = false;

void encoder_gpio_callback(uint gpio, uint32_t events) {
  if (gpio == PinCounterIn) {
    uint32_t time = time_us_32();
    uint32_t dt = time - ripplecounter_last_time;
    if (!EnableDebouncing || ripplecounter_last_dt > InactivityThresholdUs || dt * 100 > ripplecounter_last_dt * DebounceThresholdPercent) {
      if (ripplecounter_direction) ripplecounter_position--;
      else ripplecounter_position++;
    }
    ripplecounter_last_time = time;
    ripplecounter_last_dt = dt;
  }
}

void motor_set_direction(bool direction) {
  ripplecounter_direction = direction;
}

void motor_set_power(uint32_t power) {
  if (ripplecounter_direction) {
    pwm_set_chan_level(slice, pwm_gpio_to_channel(PinMotorA), PWMWrap);
    pwm_set_chan_level(slice, pwm_gpio_to_channel(PinMotorB), PWMWrap - power);
  } else {
    pwm_set_chan_level(slice, pwm_gpio_to_channel(PinMotorB), PWMWrap);
    pwm_set_chan_level(slice, pwm_gpio_to_channel(PinMotorA), PWMWrap - power);
  }
}

uint32_t motor_get_max_power() {
  return PWMWrap;
}

void ripplecounter_motor_init() {
  adc_init();
  adc_gpio_init(PinMotorISense);

  slice = pwm_gpio_to_slice_num(PinMotorA);
  pwm_set_wrap(slice, PWMWrap);

  gpio_init(PinMotorA);
  gpio_set_function(PinMotorA, GPIO_FUNC_PWM);
  gpio_init(PinMotorB);
  gpio_set_function(PinMotorB, GPIO_FUNC_PWM);
  motor_set_power(0);
  pwm_set_enabled(slice, true);

  gpio_init(PinCounterIn);
  gpio_set_dir(PinCounterIn, GPIO_IN);
  gpio_pull_down(PinCounterIn);

  gpio_set_irq_enabled(PinCounterIn, GPIO_IRQ_EDGE_FALL, true);
  gpio_set_irq_callback(&encoder_gpio_callback);
  irq_set_enabled(IO_IRQ_BANK0, true);
}

int32_t ripplecounter_get_current_ma() {
  adc_select_input(PinMotorISense - 26);
  int32_t raw_mv = (int32_t)adc_read() * 3300 / 4095 - 1650;
  return raw_mv * 10000 / CurrentSenseGain;
}

int32_t ripplecounter_get_position_counts() {
  return ripplecounter_position;
}

void ripplecounter_reset_position() {
  ripplecounter_position = 0;
}

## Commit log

2023-04-25 add pcb
    [motordriver.kicad_sch, ripplecounter-Edge_Cuts.dxf, ripplecounter-F_Courtyard.dxf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]
2023-04-28 readme and schematic
    [motordriver.kicad_sch, ripplecounter.kicad_pcb]

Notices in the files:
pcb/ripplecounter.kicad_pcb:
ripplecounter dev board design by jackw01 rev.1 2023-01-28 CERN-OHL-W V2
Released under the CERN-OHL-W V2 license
